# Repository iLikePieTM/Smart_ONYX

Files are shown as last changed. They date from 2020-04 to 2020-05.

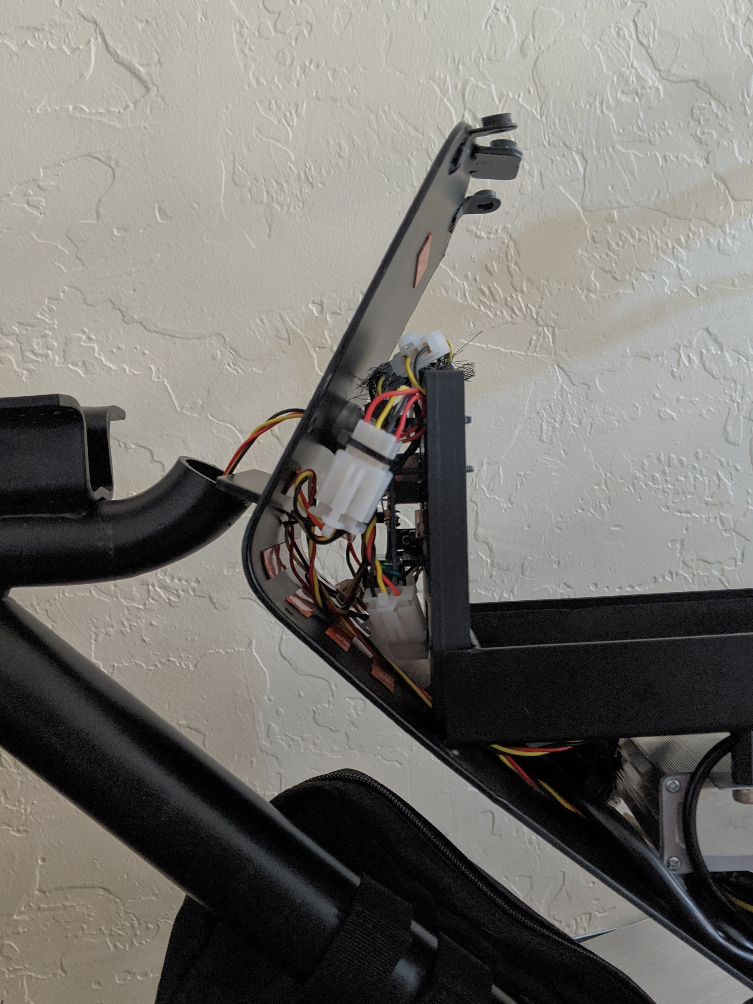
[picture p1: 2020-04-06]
Reference_Pictures/Smart ONYX_OBC Cluster_Assembled.jpg

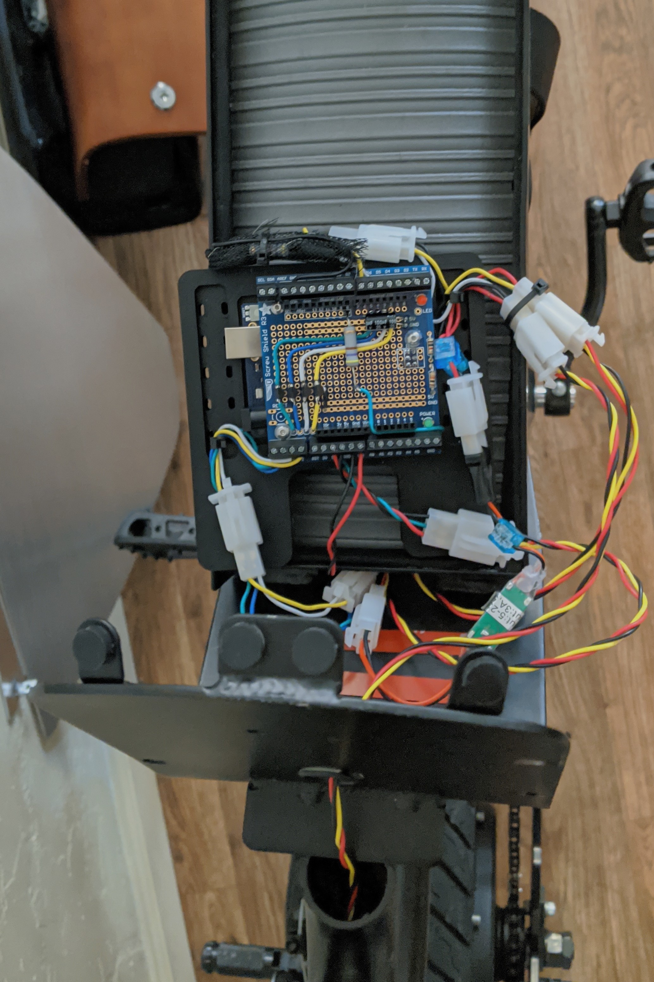
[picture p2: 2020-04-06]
Reference_Pictures/Smart ONYX_OBC Cluser_Assembly Prep.jpg

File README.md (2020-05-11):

# SMART_ONYX

### An Arduino based modification platform for the ONYX RCR electric motorbike.

The ONYX RCR is an awesome bike that I've been having a lot of fun with but it lacks some modern creature comforts. Therefore, I decided to spend way to much time designing and building mods to bring the RCR into the 21st century.

### Features:
 - Integrated signal lights via NeoPixel LED strips that combine running, turn, and break signals into a clean package.
   - Mounting: The front signals are wrapped around the headlight and back signals are supported by a custom, 3D printed bracket.
 - Underglow LEDs with multiple effects and color options.
 - CAD / STL Files for the tail light and Arduino mounts in addition to a license plate mount / fender eliminator.
 - Other features in progress:
   - Sensors: currently bike roll and temperature data are collected with the Arduino UNO Wifi Rev 2 integrated IMU. The ultimate goal is to collect additional speed, acceleration, and positional (GPS) data.
   - IoT: Another future goal to utilize a cellular shield to sync the bike telemetry with an IoT service.

## Getting Started
This is not indented as a guide but I'm making all my work available to inspire others. The file structure overview and bill of materials are located bellow and if you have any questions please reach out.

### File structure:
 - **CAD:** includes the Solidworks files (and STL files when applicable) for the physical modifications.
 - **Reference_Pictures:** includes assembly pictures, a wiring diagram, and some glamour shots.
 - **smart_ONYX:** includes all the Arduino code to run the lights, sensors, etc. See it's readme for more info.

 ### Bill of Materials *(electronics)*:
 - [Arduino UNO WiFi Rev 2](https://www.digikey.com/product-detail/en/arduino/ABX00021/1050-1166-ND/9486717)
 - [NeoPixel RGBW Strip - 1m](https://www.adafruit.com/product/2837?length=1)
 - [DC/DC Buck Converter - 5V @ 3A](https://www.adafruit.com/product/1385)
 - [L4931CZ50-AP - 5.0V Voltage Regulator](https://www.digikey.com/product-detail/en/stmicroelectronics/L4931CZ50-AP/497-5838-1-ND/1506450)
 - [BK/ATC-5 - 5A Fuse](https://www.digikey.com/product-detail/en/eaton-bussmann-electrical-division/BK-ATC-5/283-2316-ND/264840)
 - [UFW1V472MHD - 4700uF @ 35v Electrolytic Capacitor](https://www.digikey.com/product-detail/en/nichicon/UFW1V472MHD/493-3182-ND/1965204)
 - Basic electronic supplies: wires, solder, etc.

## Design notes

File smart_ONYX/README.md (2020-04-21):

# smart_ONYX: Arduino Code Overview

As mentioned in the top-level README.md, the Smart_ONYX project brings signals, sensors, and eventually IoT capabilities to the ONYX RCR. For more information, see that README.

## Getting Started

I'm going to keep this short and sweet as the code *should* be self-documenting with comments throughout. However, I would like to note that this was written for my personal use and may not be ... polished. If you would like more help getting it set up please reach out to me.

*Use it at your own risk.*

### Prerequisites

This code is written to run on an Arduino UNO WiFi Rev 2. It is mostly compatible with the Arduino UNO and other similar devices but this is not guaranteed and modifications will be necessary. If you attempt to use this code please see the **wiring diagram** included in this repository and note that modifications to the code will be necessary if you deviate from it.

### Required Libraries:
 - ```Arduino_LSM6DS3.h``` to gather data from the IMU on the WiFi Rev 2
   - **NOTE:** the current master branch of the Arduino_LSM6DS3 library *does not* support the integrated temperature sensor. I have added support to the library but (as of writing) it has not been merged. See [here](https://github.com/arduino-libraries/Arduino_LSM6DS3/pull/12).
 - ```Adafruit_NeoPixel.h``` to control of all the LEDs

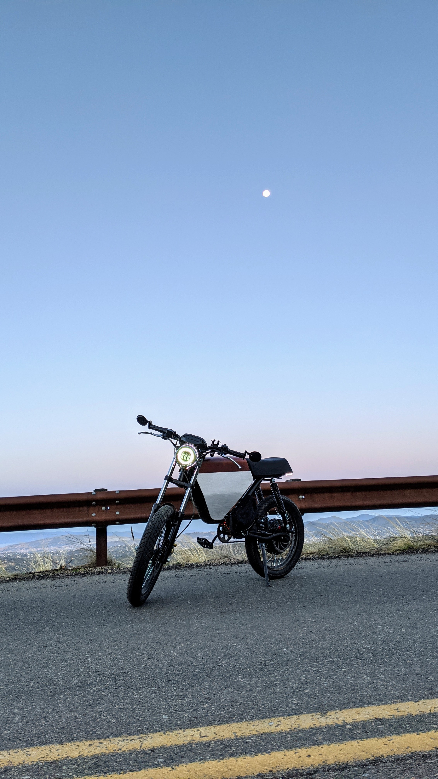
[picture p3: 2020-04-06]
Reference_Pictures/Smart ONYX_Glamour 1.jpg

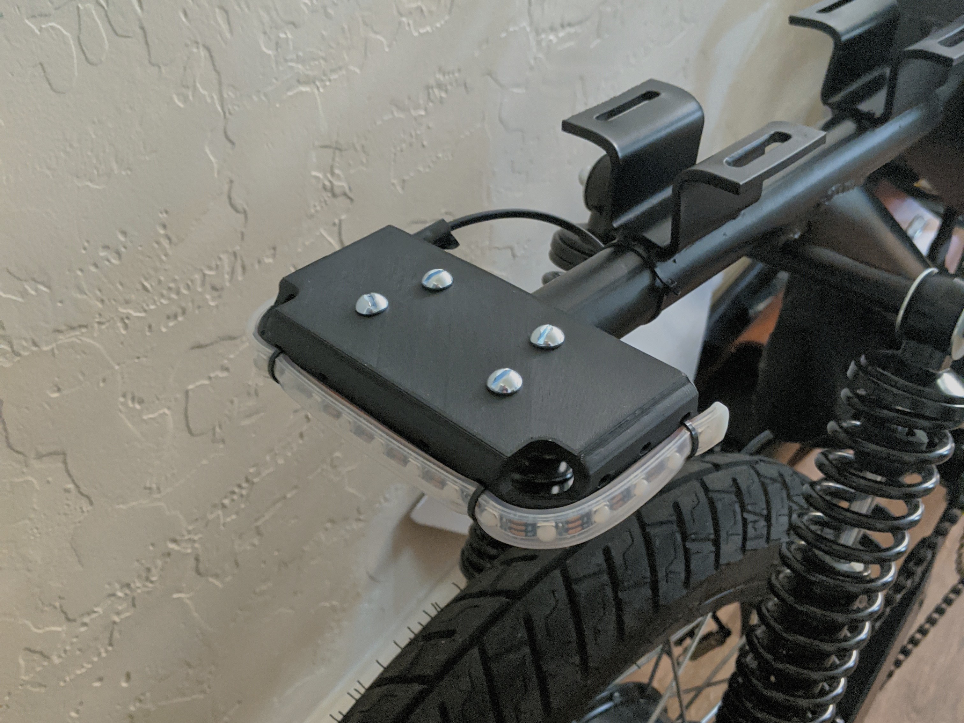
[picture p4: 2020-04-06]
Reference_Pictures/Smart ONYX_Tail Light_Mount_FD.jpg

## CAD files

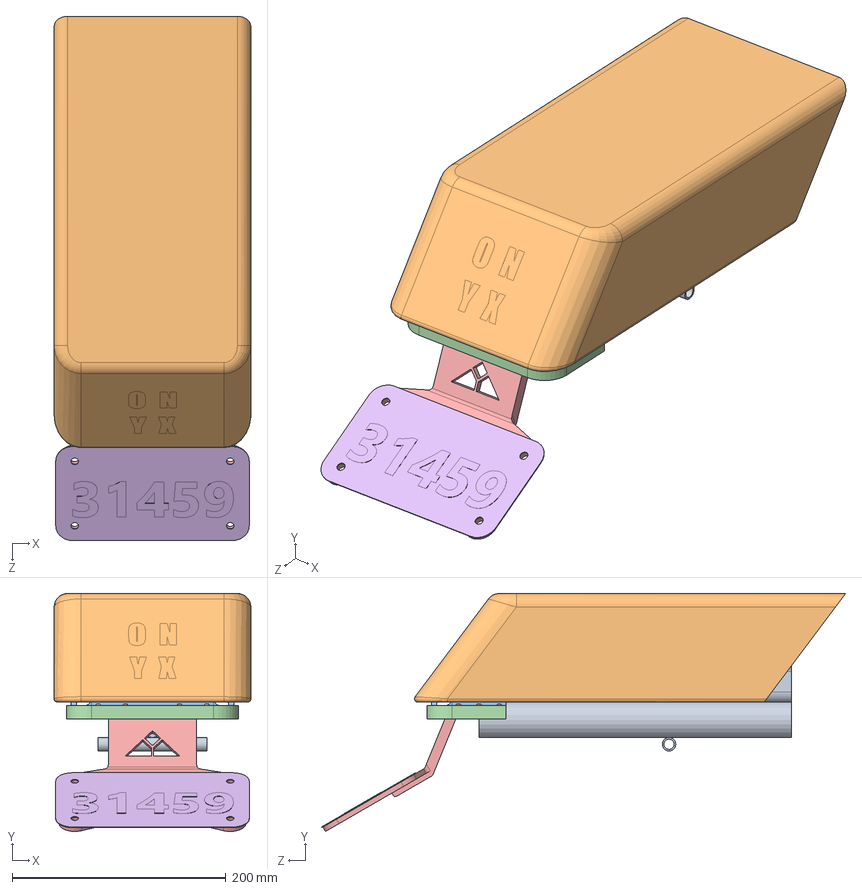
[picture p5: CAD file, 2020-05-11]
CAD/Solidworks_Files/Smart ONYX_Rear Assem.SLDASM
184.1 x 222.6 x 490.2 mm
ONYX_RCR_Seat Support
ONYX_RCR_Seat
Smart ONYX_Tail Light_Mount_FDM
Smart ONYX_Tail Light_NeoPixels
Smart ONYX_Fender Eliminator
Generic_Moped Plate

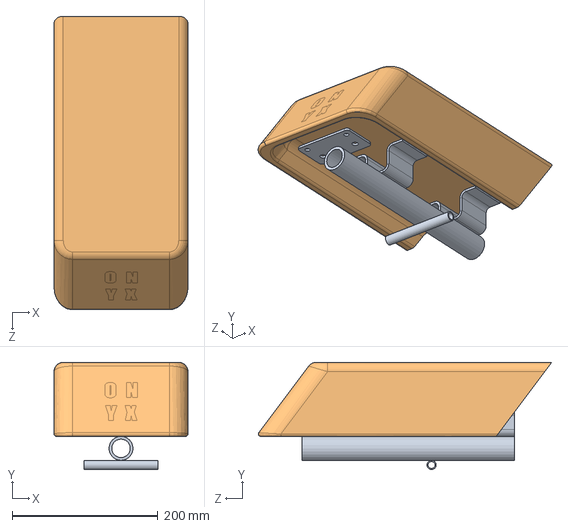
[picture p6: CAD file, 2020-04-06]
CAD/Solidworks_Files/ONYX_RCR_Seat Assem.SLDASM
184.1 x 147.3 x 403.2 mm
ONYX_RCR_Seat Support
ONYX_RCR_Seat

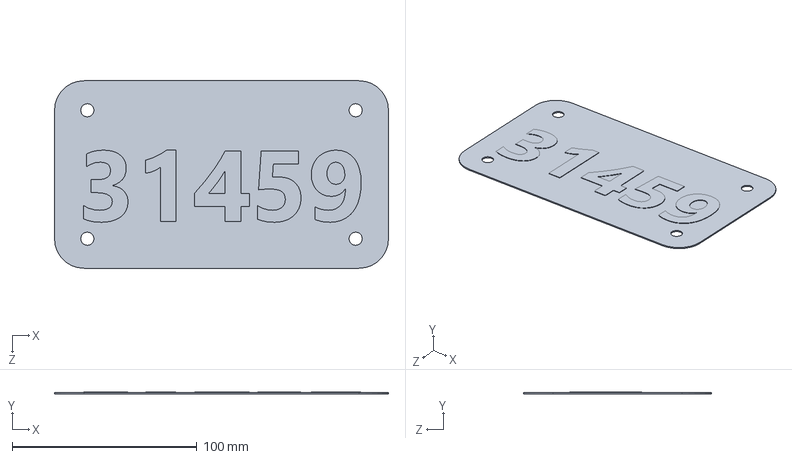
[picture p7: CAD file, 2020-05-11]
CAD/Solidworks_Files/Generic_Moped Plate.SLDPRT
181.0 x 1.02 x 101.6 mm

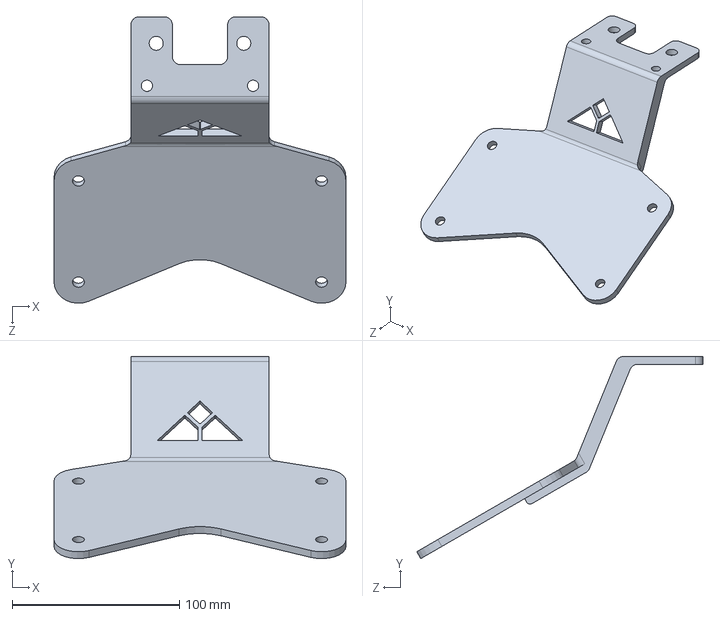
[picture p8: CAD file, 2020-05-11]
CAD/Solidworks_Files/Smart ONYX_Fender Eliminator.SLDPRT
174.6 x 121.0 x 171.3 mm

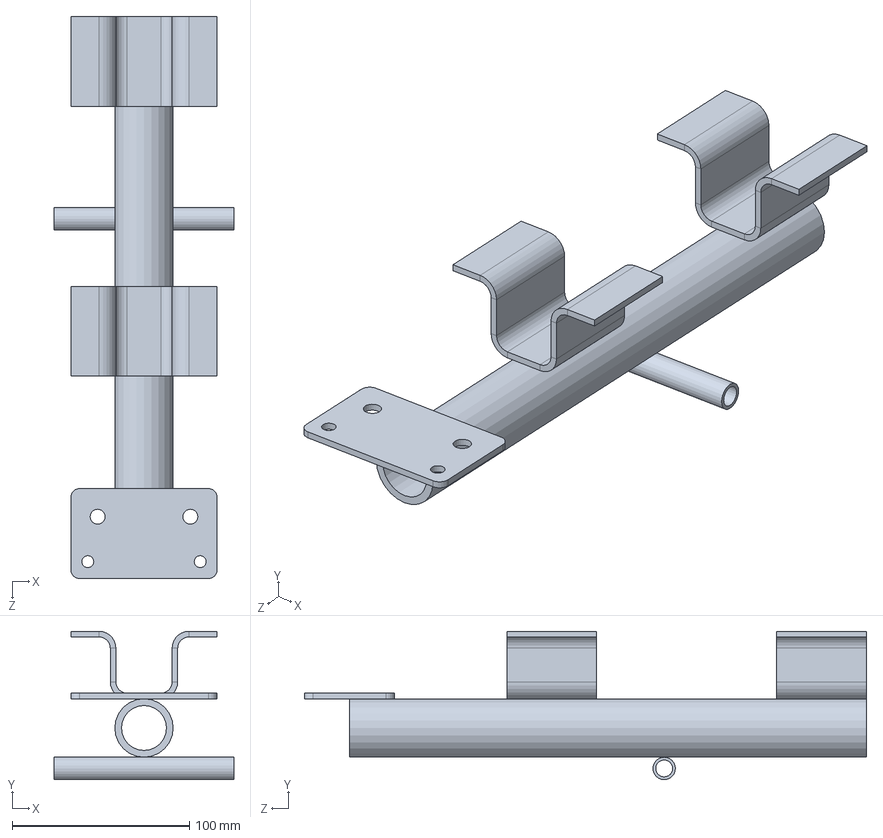
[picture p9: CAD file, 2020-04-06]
CAD/Solidworks_Files/ONYX_RCR_Seat Support.SLDPRT
101.6 x 83.8 x 317.5 mm

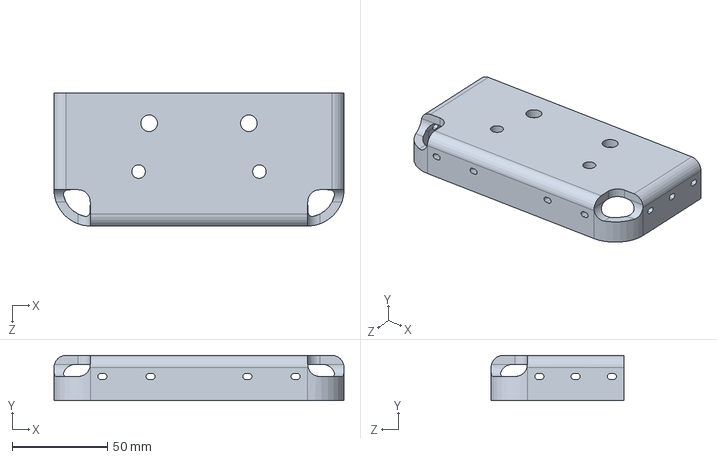
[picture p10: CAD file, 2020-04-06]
CAD/Solidworks_Files/Smart ONYX_Tail Light_Mount_FDM.SLDPRT
152.4 x 23.8 x 69.8 mm

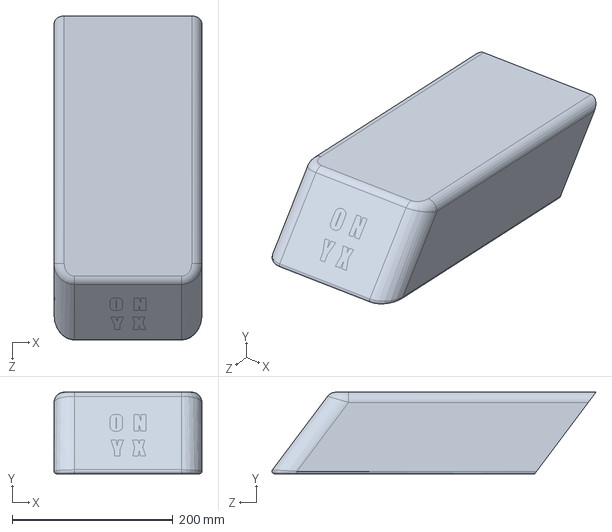
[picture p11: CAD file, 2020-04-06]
CAD/Solidworks_Files/ONYX_RCR_Seat.SLDPRT
184.1 x 101.6 x 403.2 mm

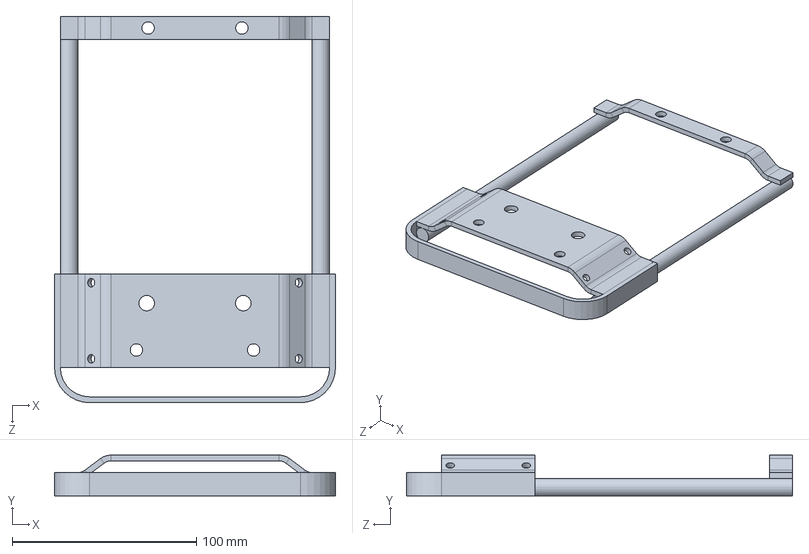
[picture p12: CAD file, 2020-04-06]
CAD/Solidworks_Files/Smart ONYX_Tail Light_Mount.SLDPRT
152.4 x 22.2 x 209.6 mm

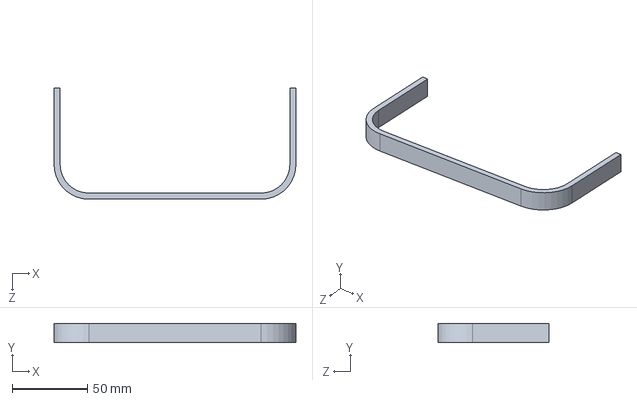
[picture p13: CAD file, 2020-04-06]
CAD/Solidworks_Files/Smart ONYX_Tail Light_NeoPixels.SLDPRT
160.5 x 12.7 x 73.9 mm

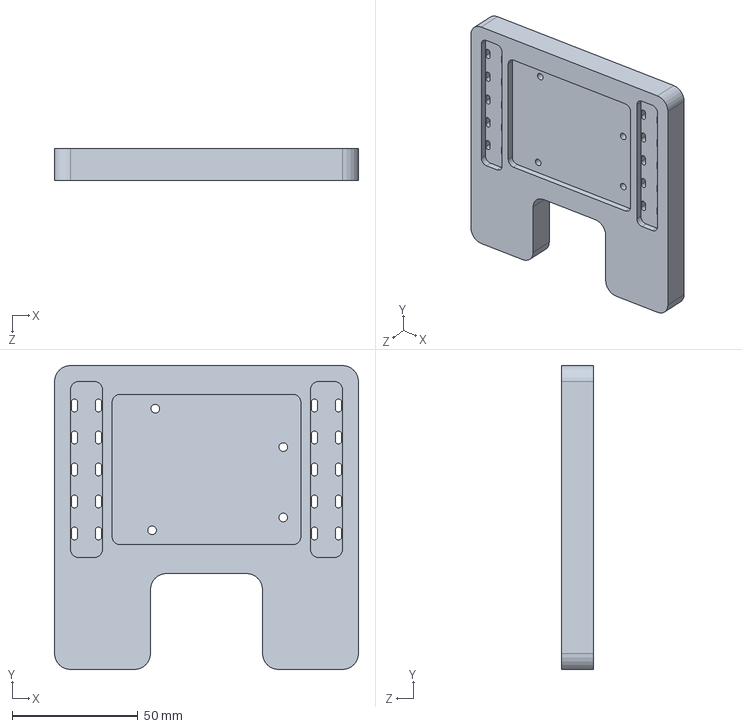
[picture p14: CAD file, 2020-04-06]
CAD/Solidworks_Files/Smart ONYX_OBC_Mount.SLDPRT
120.7 x 120.7 x 12.7 mm

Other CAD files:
CAD/STL_Files/Smart ONYX_Fender Eliminator.STL
CAD/STL_Files/Smart ONYX_OBC_Mount.STL
CAD/STL_Files/Smart ONYX_Tail Light_Mount_FDM.STL

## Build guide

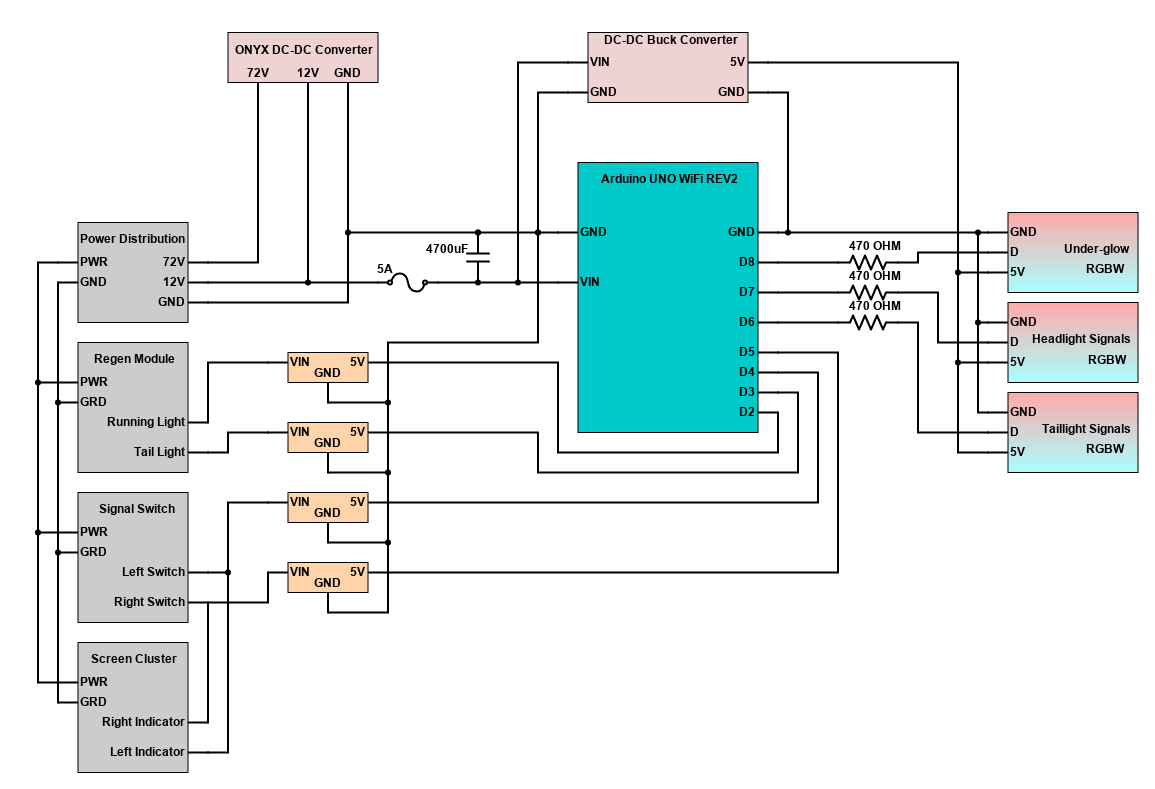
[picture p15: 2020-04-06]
Reference_Pictures/Smart ONYX_Wiring Diagram.png

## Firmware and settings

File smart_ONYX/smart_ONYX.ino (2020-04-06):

/*
   smart_ONYX
   Adding "smart" capabilities to the ONYX RCR with an Arduino.

   Alex Hoppe (c) 2020
   Updated: 4/3/2020
*/


// Libraries:
#include <Arduino_LSM6DS3.h>      // Integrated IMU
#include <Adafruit_NeoPixel.h>    // RGBW LED controll


// Global Constants:
const int RUNNING_SIGNAL = 2;     // Input pins from ONYX
const int BRAKE_SIGNAL = 3;       // - See wiring diagram
const int LEFT_SIGNAL = 4;
const int RIGHT_SIGNAL = 5;

const int TAIL_LEDS = 6;          // Neopixel output pins
const int HEAD_LEDS = 7;
const int GLOW_LEDS = 8;

const int NUM_TAIL_LEDS = 18;      // Number of LEDS in each strip
const int NUM_HEAD_LEDS = 23;
const int NUM_GLOW_LEDS = 10;

const int SIGNAL_BRIGHTNESS = 196; // Max LED brightness
const int GLOW_BRIGHTNESS = 128;


// Glabal Variables:
unsigned long deltaT = 0;
bool bikeOn = false;
String bikeTelemetry = "";


// Declare the NeoPixel strip objects (Really GRBW order)
Adafruit_NeoPixel tailStrip(NUM_TAIL_LEDS, TAIL_LEDS, NEO_RGBW + NEO_KHZ800);
Adafruit_NeoPixel headStrip(NUM_HEAD_LEDS, HEAD_LEDS, NEO_RGBW + NEO_KHZ800);
Adafruit_NeoPixel glowStrip(NUM_GLOW_LEDS, GLOW_LEDS, NEO_RGBW + NEO_KHZ800);


// Declare functions:
void bikeSignals(Adafruit_NeoPixel *tailStrip, Adafruit_NeoPixel *headStrip, bool bikeOn = true);
bool calculateTelemetry(String &telemetryData);
void underGlow(Adafruit_NeoPixel *glowStrip, int effect, bool bikeOn = true);


void setup() {
  // Start Serial for debuging
  Serial.begin(9600);

  // Define pin mogdes
  pinMode(RUNNING_SIGNAL, INPUT);
  pinMode(BRAKE_SIGNAL, INPUT);
  pinMode(RIGHT_SIGNAL, INPUT);
  pinMode(LEFT_SIGNAL, INPUT);

  // Initalize the NeoPixel Strips
  tailStrip.begin();
  tailStrip.setBrightness(SIGNAL_BRIGHTNESS);
  tailStrip.show();
  headStrip.begin();
  headStrip.setBrightness(SIGNAL_BRIGHTNESS);
  headStrip.show();
  glowStrip.begin();
  glowStrip.setBrightness(GLOW_BRIGHTNESS);
  glowStrip.show();

  // Start the IMU
  IMU.begin();
}


void loop() {
  // Grab the current elpased time
  deltaT = millis();

  // Find all the bike telemetry data
  if (calculateTelemetry(bikeTelemetry)) {
    //Serial.println(bikeTelemetry);
  }

  // Is the bike on?
  if (digitalRead(RUNNING_SIGNAL) == HIGH) {
    bikeOn = true;
    bikeSignals(&tailStrip, &headStrip);
    underGlow(&glowStrip, 2);
  } else if (bikeOn) {
    // If the bike was just turned off, save power by turning the lights off
    bikeOn = false;
    bikeSignals(&tailStrip, &headStrip, bikeOn);
    underGlow(&glowStrip, 0, bikeOn);
  }
  
}

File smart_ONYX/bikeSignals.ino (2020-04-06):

/*
   bikeSignals
   Controls the bike's running, tail, and signal lights during standard driving operation
   - Accepts a pointer to a tailStrip and headStrip NeoPixel object
   - Optional bool argument can be passed to turn everything off

   Alex Hoppe (c) 2020
   Updated: 3/16/2020
*/

void bikeSignals(Adafruit_NeoPixel *tailStrip, Adafruit_NeoPixel *headStrip, bool bikeOn) {
  // Define Internal timekeeping
  static unsigned long brakeStartT = 0;
  static unsigned long signalStartT = 0;

  if (bikeOn) {

    // The running light should always be on and can be overwritten latter
    tailStrip->fill(tailStrip->Color(0, 0, 64, 96), 0, NUM_TAIL_LEDS);
    headStrip->fill(headStrip->Color(0, 0, 64, 96), 0, NUM_HEAD_LEDS);

    // Are the brakes being activated?
    if (digitalRead(BRAKE_SIGNAL) == HIGH) {
      flashyBrake(tailStrip, brakeStartT);
    } else {
      // If the brakes aren't on, update the time
      brakeStartT = deltaT;
    }

    // Are the turn signals on?
    if (digitalRead(LEFT_SIGNAL) == HIGH || digitalRead(RIGHT_SIGNAL) == HIGH) {
      signalSnake(tailStrip, digitalRead(LEFT_SIGNAL), signalStartT);
      signalSnake(headStrip, digitalRead(LEFT_SIGNAL), signalStartT);
    } else {
      // If the signals aren't on, update the time
      signalStartT = deltaT;
    }

  } else {
    tailStrip->fill(tailStrip->Color(0, 0, 0, 0), 0, NUM_TAIL_LEDS);
    headStrip->fill(headStrip->Color(0, 0, 0, 0), 0, NUM_HEAD_LEDS);
  }

  // Push color data to the strips
  tailStrip->show();
  headStrip->show();
}


// Flashes the brake lights when first activated then produces a stead output
void flashyBrake(Adafruit_NeoPixel *strip, unsigned long brakeStartT) {
  static const int FLASH_LENGTH = 1000;
  int redIntensity;

  // Is it in the inital flashy time?
  if (deltaT - brakeStartT <= FLASH_LENGTH) {
    redIntensity = 128 + 127 * cos((deltaT - brakeStartT) * 3.1459 * 4 / FLASH_LENGTH);
  } else {
    redIntensity = 255;
  }

  // Assigns the brake intensity to the strip
  strip->fill(strip->Color(4, redIntensity, 0, 4), 0, strip->numPixels());
}


// Creates a bi-directional snake effect when the passed a NeoPixel strip
// - When snakeMag is HIGH/1 it will flow left, else right
// - Note: it assumes the Neopixel data line is attached to the left side
void signalSnake(Adafruit_NeoPixel *strip, int snakeMag, unsigned long signalStartT) {
  static unsigned const int SIGNAL_INTERVAL = 1250;
  static unsigned long deltaSignal = 0;
  static int signalCounter = 0;

  uint32_t signalColor = strip->Color(64, 255, 0, 16);
  int signalLength = strip->numPixels();
  int startPixel;

  // Determines the start point and length of the signal for even or odd strips with left or right signals
  if (signalLength % 2) {
    signalLength = signalLength / 2;
    startPixel = signalLength;
  } else {
    signalLength = signalLength / 2 - 1;
    if (snakeMag) {
      startPixel = signalLength;
    } else {
      startPixel = signalLength + 1;
    }
  }

  // Is this a new signal event or a continuation of one?
  if (deltaSignal < signalStartT) {
    deltaSignal = signalStartT;
    signalCounter = 0;
  }

  // Ensure the animation speed is perportional to the strip length
  if (deltaT - deltaSignal >= SIGNAL_INTERVAL / signalLength) {
    if (signalCounter < signalLength) {
      signalCounter++;
    } else {
      signalCounter = 0;
    }
    // Update the time since a signal change
    deltaSignal = deltaT;
  }

  // Assigns values to the LEDs in the desired direction
  if (snakeMag == HIGH) {
    for (int i = startPixel; i >= (startPixel - signalCounter); i--) {
      strip->setPixelColor(i, signalColor);
    }
  } else {
    for (int i = startPixel; i <= (startPixel + signalCounter); i++) {
      strip->setPixelColor(i, signalColor);
    }
  }

}

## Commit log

2020-04-06 Initial commit!
    [Generic_Moped Plate.SLDPRT, ONYX_RCR_Seat Assem.SLDASM, ONYX_RCR_Seat Support.SLDPRT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]
2020-05-11 Added Fender Eliminator CAD
    [Generic_Moped Plate.SLDPRT, Smart ONYX_Fender Eliminator.SLDPRT, Smart ONYX_Fender Eliminator.STL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]
